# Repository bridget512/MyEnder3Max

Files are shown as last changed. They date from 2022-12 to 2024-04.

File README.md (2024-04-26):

# MyEnder3Max (2020 model)

!! DO NOT JUST COPY CONFIGURATIONS TO YOUR PRINTER AND EXPECT IT TO BE OK !!

Read through the files and make sure they are suitable for YOUR machine. I'm constantly changing and modifying the machine so configurations are specific to MY machine.

Please be careful, and I hope you find something useful :)

### Do your own calibrations for: 
- PID tuning, Z-Offset, Extruder E-steps/rotation, Pressure Advance. (Recommend OrcaSlicer Calibration methods)
- InputShaper, BLTouch XY offset
- Check stepper motor current. Stock: XYZ = 0.580, E = 0.650

## Modifications - Hardware
- BigTreeTech SKR Mini E3 Version 3.0
- Klipper Firmware on a Raspberry Pi 3b running Fluidd UI + rPi camera
- BL Touch v3.1: "Auto Bed Leveling"
- Belted-Z modification using Dual Steppers on a Single Driver. Based on 2 Voron M4 Extruder Kits and adapted for use on the Z-Axis.
- Belted-Z plate accepts a Voron M4 Extruder to be attached using two printable standoffs that also hold the X-Axis umbilical cables.
- Switchwire based Y-Axis modification. Adapted to use a geared 20T GT2 6mm Pulley and M5 bolt.
- Voron M4 Extruder
- Bi-Metal HeatBreak: Generic $20 (Titanium + Copper) w/standard creality heatsink
- HeroMe 7 Hotend Cooler w/Noctua 4020 Fan
- HeroMe 7 5015 Dual Part Cooler
- All printed parts using ASA

## Modifications - Software and Other
- KAMP - Adaptive bed leveling that runs at the begining of every print for perfect bed mesh's where you're printing.
- InputShaper: ADXL345 + Calibration Macros.
- Firmware Retraction [Must also be enabled in slicer. Cura needs a plugin]: Realtime fine tuning of retraction settings.
- Exclude Object [Objects must be labeled in slicer]: Allows individual objects being printed to be excluded from future printing moves. 
- Creality Enclosure - Large (Fabric)
- Raspberry Pi Camera - Auto feed start via script

## Disabled Features:
- Filament Runout (Remove comments to re-enable)

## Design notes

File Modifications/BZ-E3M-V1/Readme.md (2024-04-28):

# M4 Belted Z Modification - V1R1

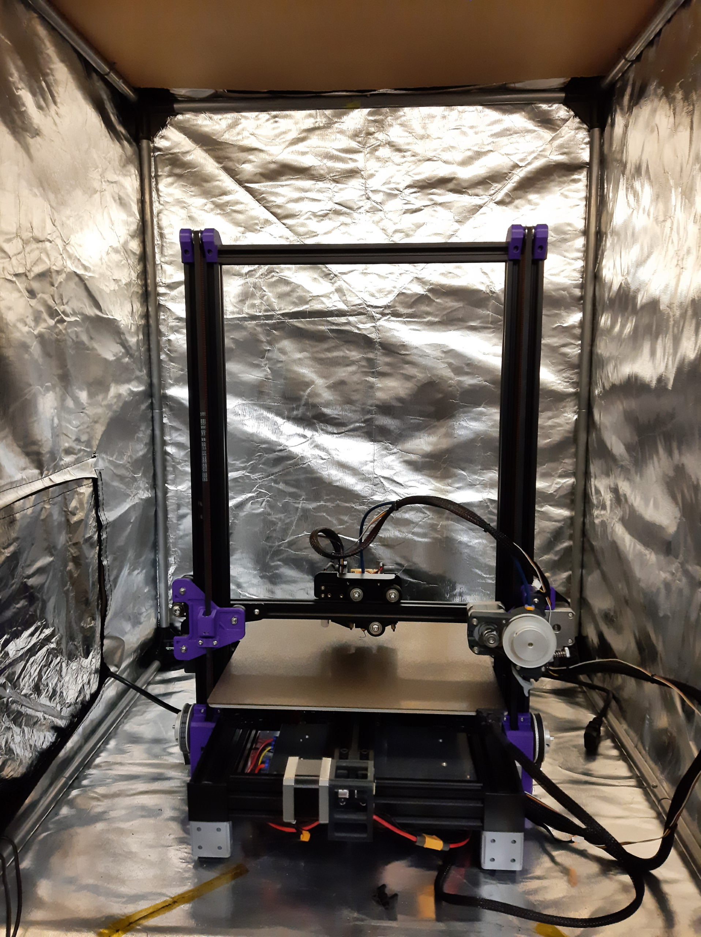
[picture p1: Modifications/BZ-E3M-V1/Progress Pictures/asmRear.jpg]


## Components Used:
- 2x Voron M4 Extruder Kits
    - Uses some of the parts (Bearings, some screws, 80t drive gear pulley and screws).
    - Spare extruder gears are great when printing CF filaments as they get worn down! ;)
    - Future versions will use more of the parts in the kit.
- 2x 60mm x 5mm D-Shafts (Voron 2.4 Z-Drive/D-Axis Kit)
    - Currently using these shafts instead of the extruder kit shafts due to the shaft notches being in awkward spots. 
- 2x 30mm x 5mm dowel pins
    - These are used for the top pulleys.
- 28x 5mmID x 1mm spacers
    - Future versions will use printed spacers.
- Pulleys:
    - 2x Idler Pulley - GT2, 20 Teeth, 5mm Bore, 6mm Width .
    - 2x Timing Pulley Sprocket - GT2, 20 Teeth, 5mm Bore, 6mm Width (+2 if printing 80t reduction gear).
- Screws:
    - 6x M3x6
    - 4x M3x8
    - 4x M3x10
    - 6x M3x12 (2 from M4 Kit)
    - 4x M3x16 (M4 Kit)
    - 4x M3x30 (M4 Kit)
    - 2x M3x35
    - 3x M5x40
- Belt: 2m GT2 Gates 6mm wide

# BZ-V1 Assembly Notes 
Please note that this is not a completed modification and is very much a mixture of parts. 

The following notes were taken when assembling the kit and will be used to make modifications to the parts for future revisions.

## Material and Settings
 - Material: ASA - Purple Siddament. 
 - Temps: H:255c, B: 98.
 - Part: 4 Walls, 5 Tops/Bottoms, 40% infill.
 - Speeds: 60mm/s walls/infill, 40mm/s default.
 - Accelerations: 1500-3000.

## BZ-MP (Motor Plates)
- Access slot for pulley should be relocated to the side (bottom access is difficult)
- Mating Faces to extrusion must be filed flat due to print orientation
- Slight movement from assembly body once mounted. This is fine.
 ### Components (Per Side)
  - 2pc M3x12, 1pc M3x6
  - Spacers 5 + 5 + 4

## BZ-M4 & BZ-R (V-Wheel Plates)
 - V-Roller Holes and Nut too small by ~0.08ish
 - Heat-Set threads not deep enough by 0.8 - 1.0mm.
 - Belt adjuster captive nut hole too small in all directions, including inner hex shape.
 - Fillet on belt adjuster causing overhang issues, make them square.
 ### Components
  - 3pc M5x40
  - 8.4mm worth of spacers (they're usually not accurate, I have 9pcs of 1mm spacers that measure 8.42mm)
  - Belt Adjuster: 1pc M3x16, 2pc M3x10

## BZ-Idlers
 - Extrusion sizing could be slightly bigger for easier fitment.
 ### Components (Per Side)
  - 1pc 30mm x 5mm dowel pin
  - 2pc M3x6, 2pc M3x8
  - 4pc M3 T-Slot Nuts

## BZ-M4-Risers
 - M3 hole too small. 

## BZ-M4-Riser-CableClamps
 - Slight layer drooping on M3 hole from overhang due to print orientation. Hole needs to be filled or enlarged in the model.
 ### Components (Per Riser)
  - 1pc M3x35

## Belt Used
- 198.5mm - 6mm - GT2 Gates

# Images
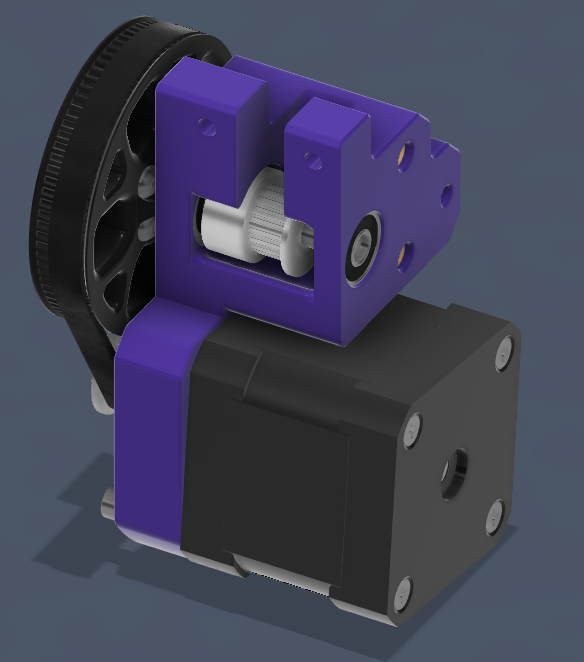
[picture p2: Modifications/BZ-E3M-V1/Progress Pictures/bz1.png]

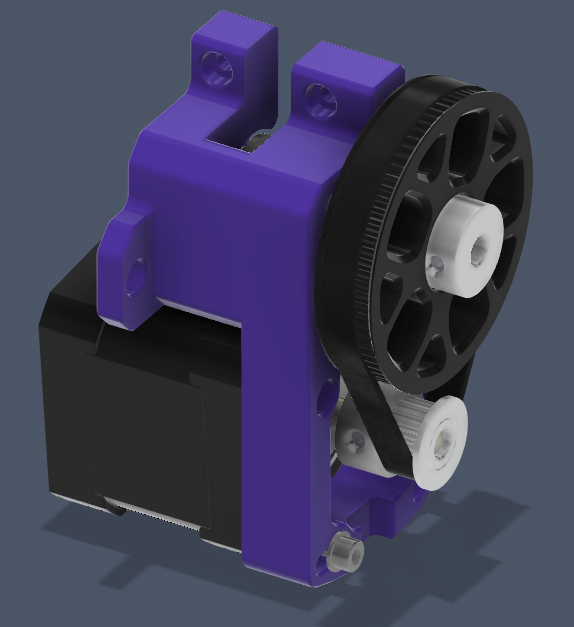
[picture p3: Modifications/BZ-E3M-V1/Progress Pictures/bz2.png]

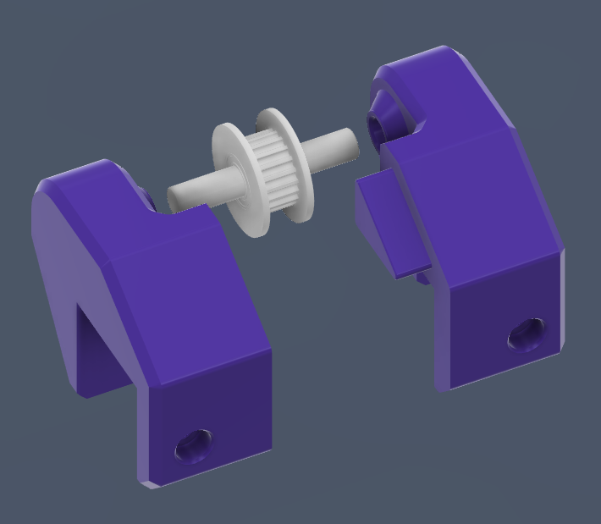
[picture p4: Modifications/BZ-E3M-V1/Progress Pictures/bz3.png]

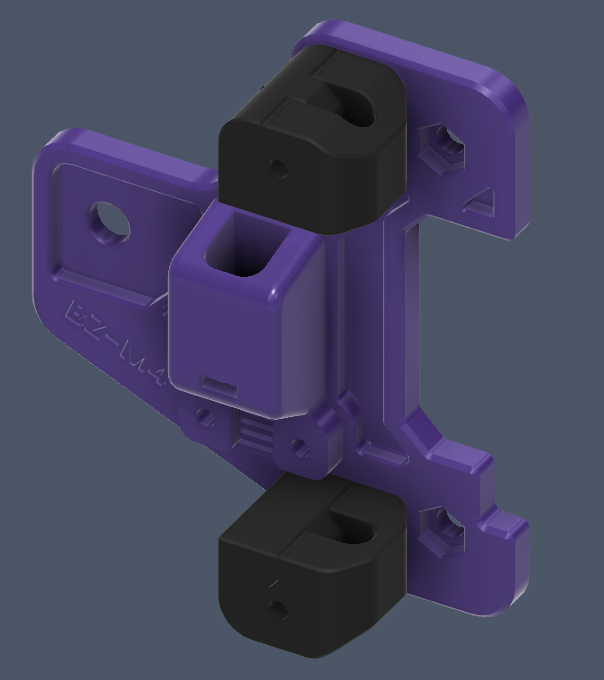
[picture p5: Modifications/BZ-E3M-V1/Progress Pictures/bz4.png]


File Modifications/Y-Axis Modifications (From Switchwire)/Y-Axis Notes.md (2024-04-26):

## Y axis
- less belt length is needed than the standard E3Max. Re-crimping the belt is necessary 

## Y axis rear notes

- The stepper attached pulley must be removed to tighten a mounting bolt placed behind the pulley.

- The motor mount bracket is very close to the build plate. It is possible that the insulation underneath the bed can catch on the bracket and pull it back. I recommend using kapton tape to stick this down to make this less likely. 

- I have concerns of heat related part failure, or parts becoming loose due to printed parts compressing and losing tension over time due to extra heat in the area.

## Y Axis Front

- ender3v2 switchwire conversion issue: Pulley bolt is an M5 bolt, the E3Max uses a M3 bolt. Modifying the adjustable carriage is needed to use this hardware. Alternatively, purchasing an idler pulley with a larger internal diameter would work.

- Slipping the belt into the printer bed plate can be difficult as there is little slack when the Y-Axis is fully assembled. Removing the front assembly, leaving the idler-pulley part attached, and bringing the bed forward makes this much easier to access and gives adequate slack.

- The current offset of the Idler body part is about 4cm shorter than the standard bracket. This reduces the amount of movement the y axis can slide on, resulting in ~4cm of build area being removed on this axis.

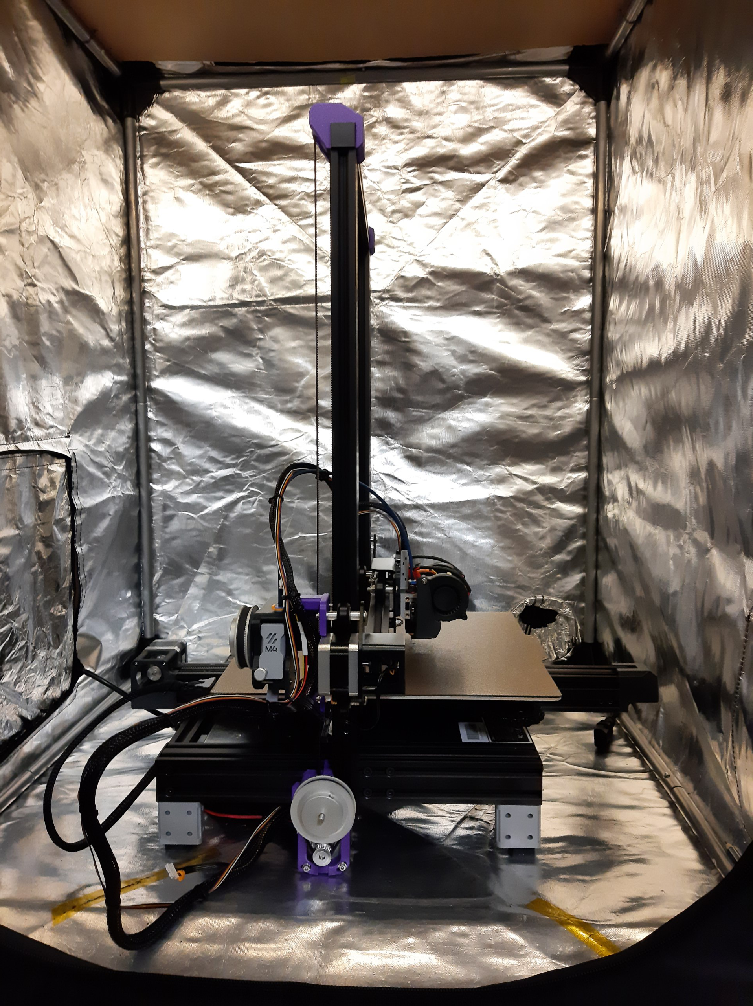
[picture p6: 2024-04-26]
Modifications/BZ-E3M-V1/Progress Pictures/asmLeft.jpg

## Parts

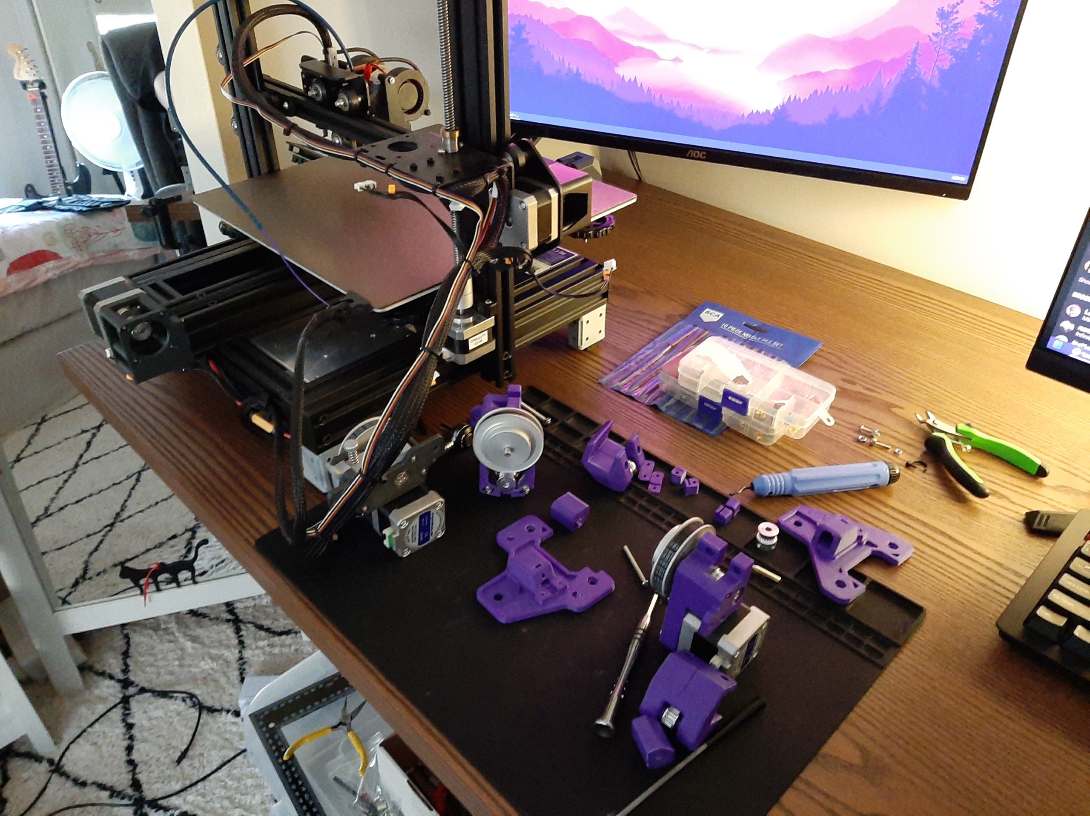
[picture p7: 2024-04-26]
Modifications/BZ-E3M-V1/Progress Pictures/Parts.jpg

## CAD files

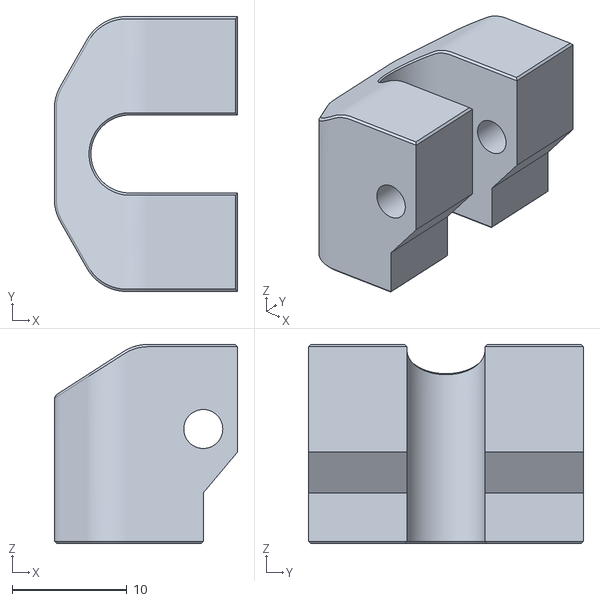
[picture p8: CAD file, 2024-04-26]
Modifications/BZ-E3M-V1/Parts/M4-Riser-CableClamp-Top-Part2.stl
16.0 x 24.0 x 17.4

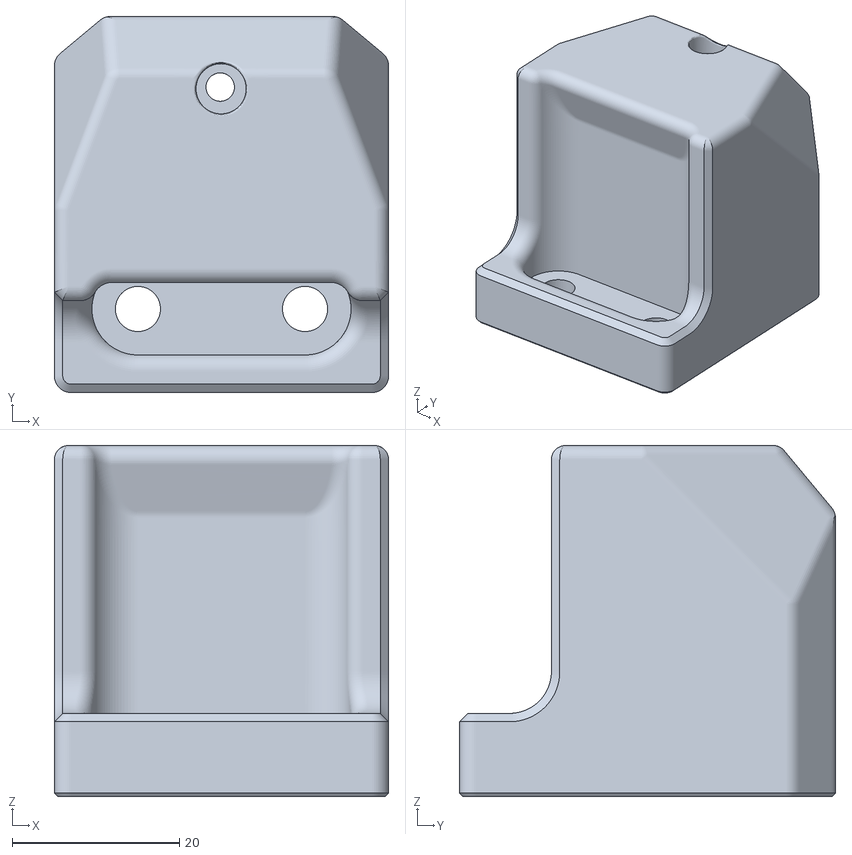
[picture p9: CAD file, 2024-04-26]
Modifications/Y-Axis Modifications (From Switchwire)/STL's/y_idler_a.stl
40.0 x 45.0 x 42.0

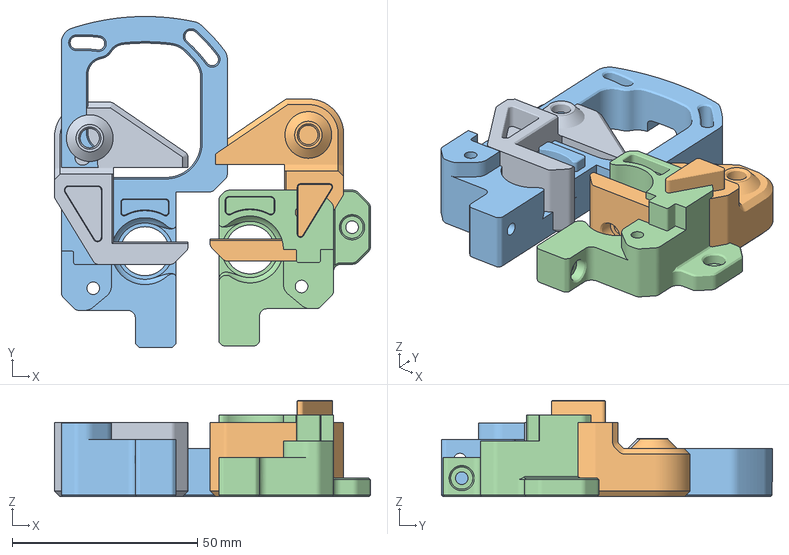
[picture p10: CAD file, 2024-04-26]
Modifications/BZ-E3M-V1/Parts/Z Mod Project.3mf
85.4 x 89.3 x 26.0 mm
TopIdlerBracketA.stl
TopIdlerBracketB.stl
ZMotorPlate_A_BottomLeft.stl
ZMotorPlate_B_BottomLeft.stl

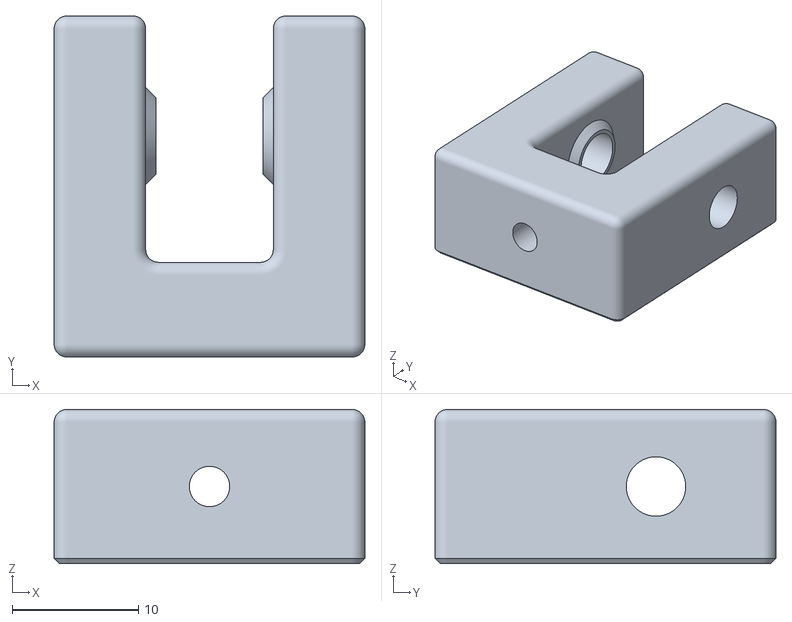
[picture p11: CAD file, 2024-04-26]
Modifications/Y-Axis Modifications (From Switchwire)/STL's/Y-Idler-M5-Geared-0.4WiderForFiling.stl
24.6 x 27.0 x 12.2

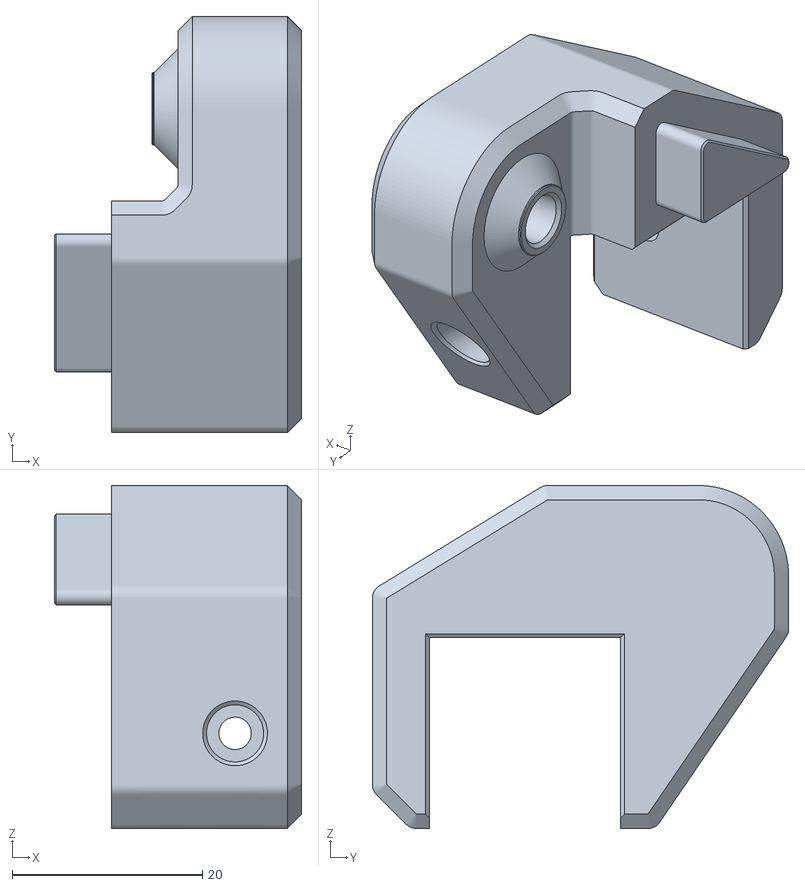
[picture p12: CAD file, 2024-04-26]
Modifications/BZ-E3M-V1/Parts/BZ-Idler-Right.stl
26.0 x 43.8 x 36.0

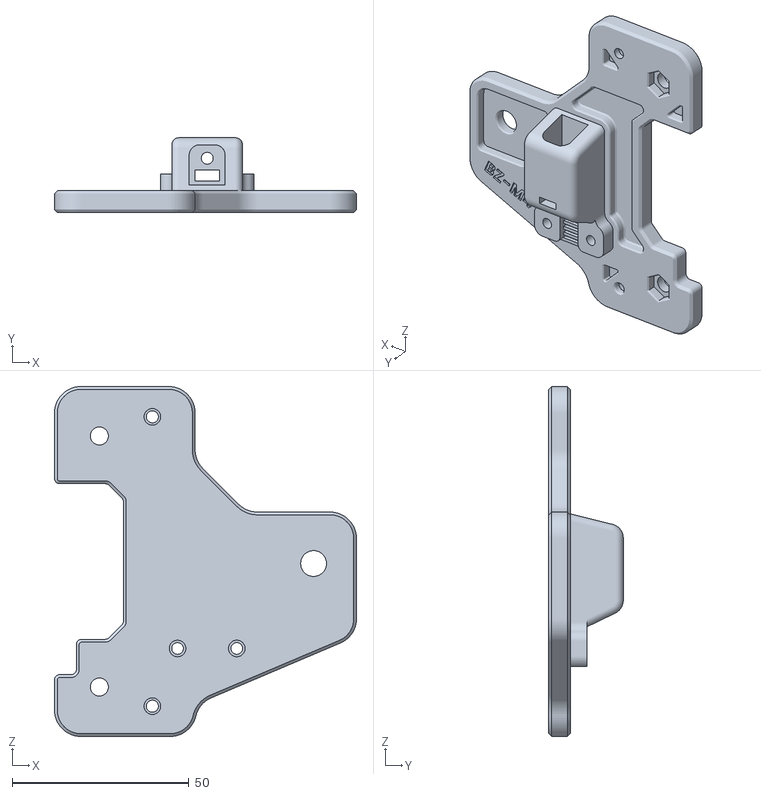
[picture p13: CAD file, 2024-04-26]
Modifications/BZ-E3M-V1/Parts/BZ-M4.stl
85.5 x 21.1 x 99.0

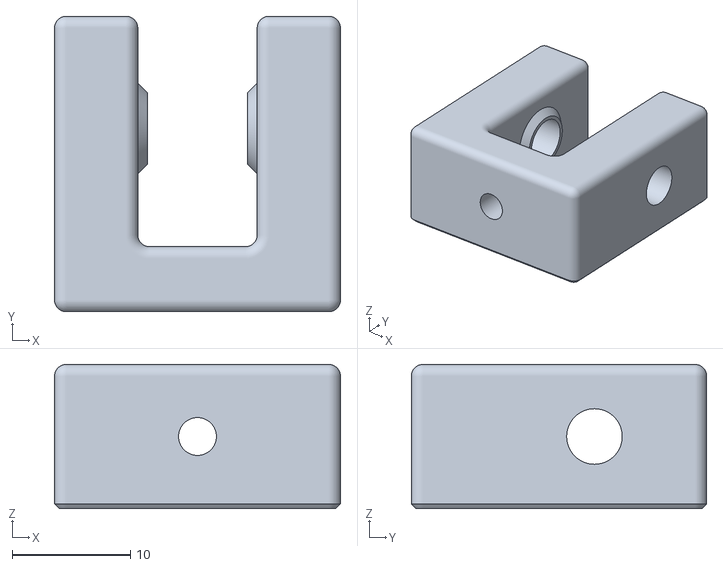
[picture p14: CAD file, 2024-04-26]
Modifications/Y-Axis Modifications (From Switchwire)/STL's/Y-Idler-M5-Geared.stl
24.2 x 25.0 x 12.2

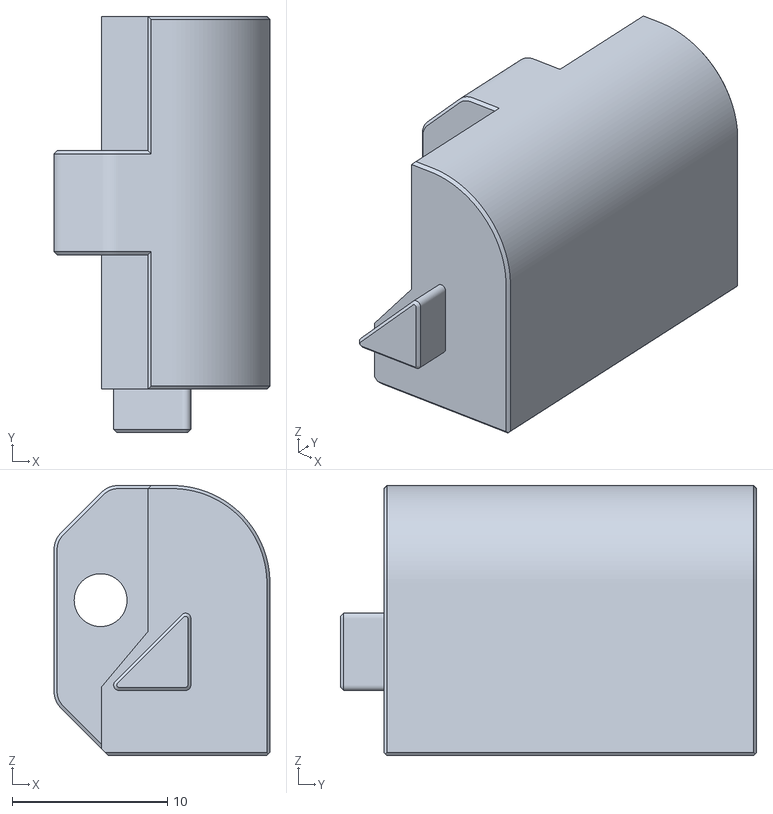
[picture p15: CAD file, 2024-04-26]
Modifications/BZ-E3M-V1/Parts/M4-Riser-CableClamp-Top-Part1.stl
13.9 x 26.8 x 17.4

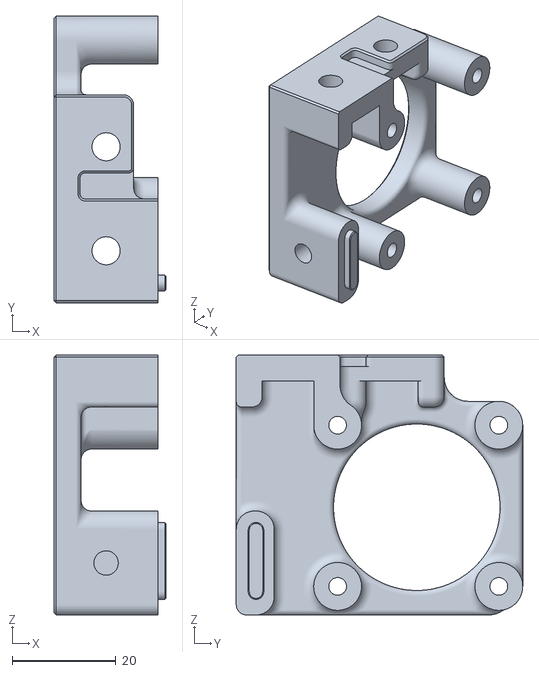
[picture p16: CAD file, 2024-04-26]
Modifications/Y-Axis Modifications (From Switchwire)/STL's/y_motor_mount_a.stl
21.5 x 55.1 x 50.0

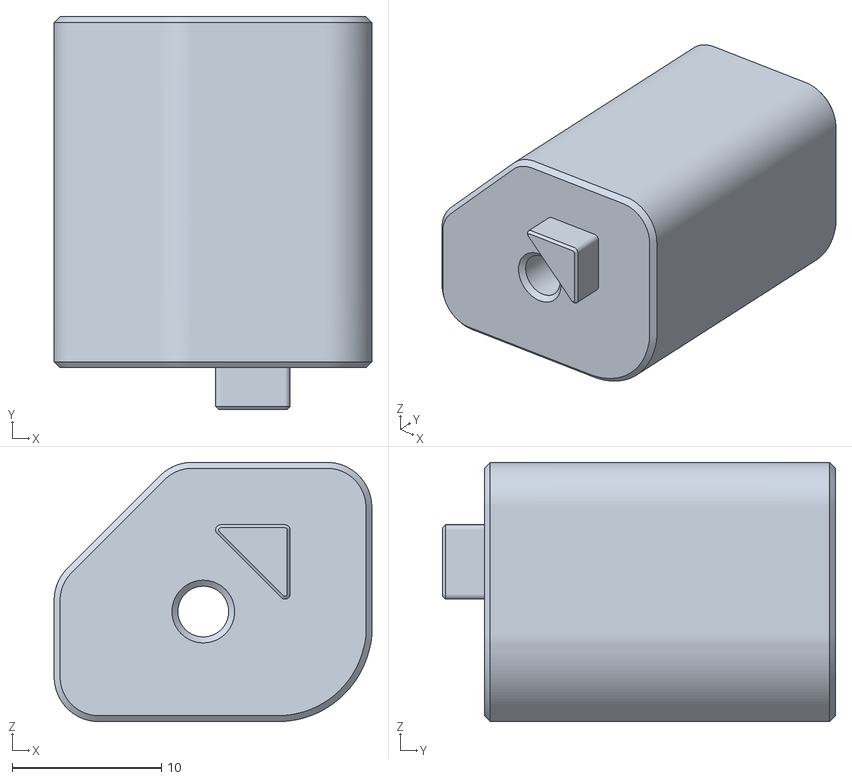
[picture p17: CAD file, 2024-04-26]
Modifications/BZ-E3M-V1/Parts/BZ-M4-RiserBottom.stl
21.3 x 26.3 x 17.4

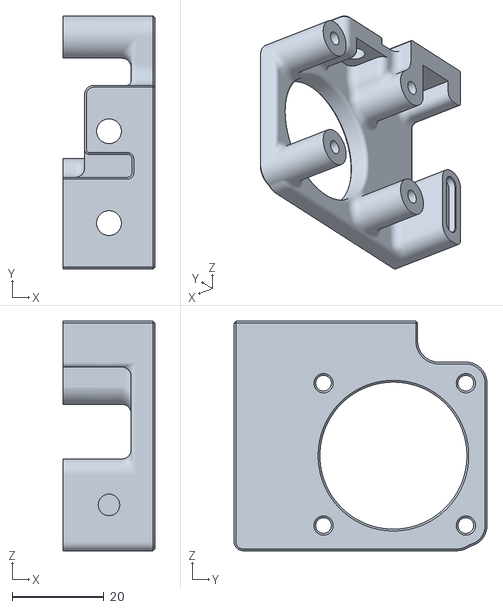
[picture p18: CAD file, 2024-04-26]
Modifications/Y-Axis Modifications (From Switchwire)/STL's/y_motor_mount_b.stl
20.0 x 55.1 x 50.0

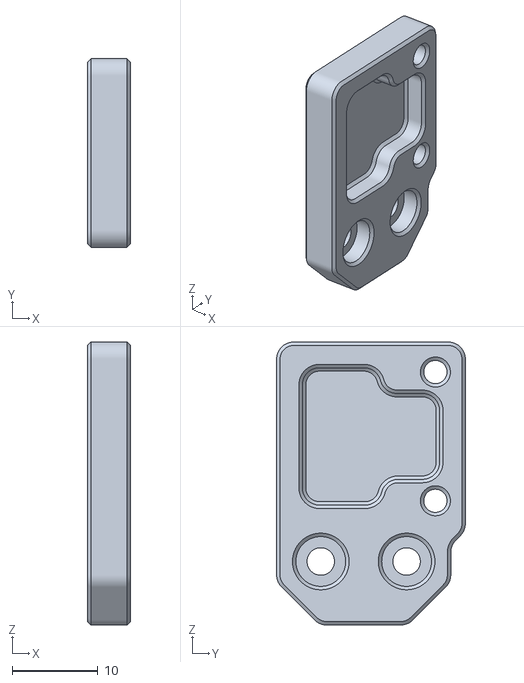
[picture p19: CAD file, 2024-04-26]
Modifications/Y-Axis Modifications (From Switchwire)/STL's/Y-Endstop.stl
5.00 x 22.0 x 33.0

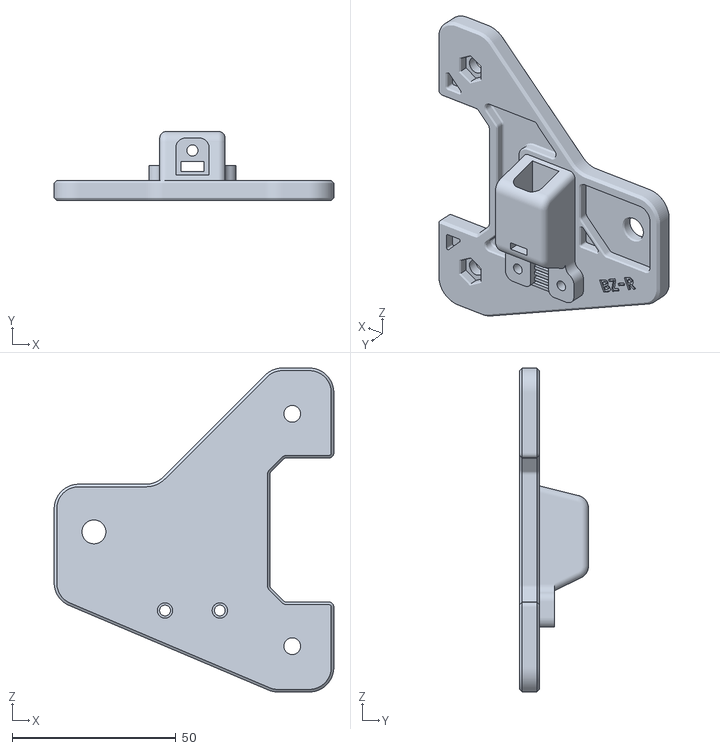
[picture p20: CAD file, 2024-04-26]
Modifications/BZ-E3M-V1/Parts/BZ-R.stl
85.5 x 21.1 x 99.0

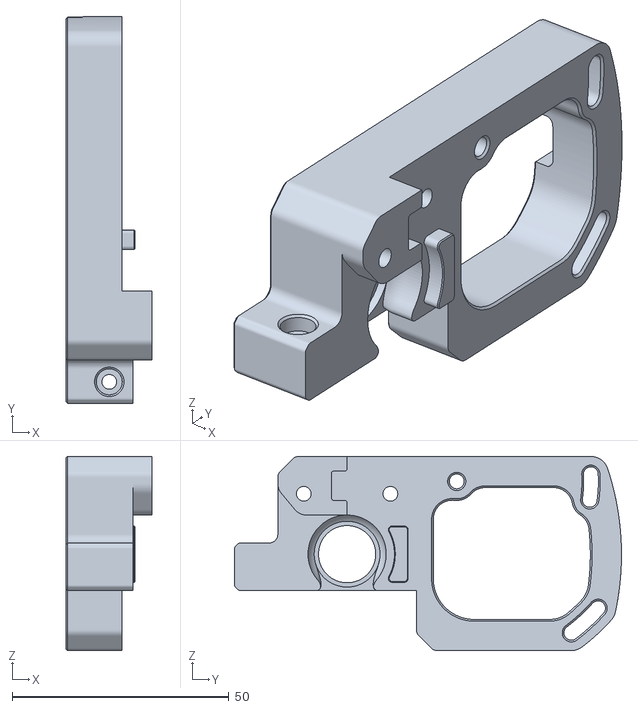
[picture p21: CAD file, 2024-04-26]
Modifications/BZ-E3M-V1/Parts/BZ-MPA.stl
19.9 x 89.3 x 44.8

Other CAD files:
Modifications/BZ-E3M-V1/Parts/M4-Riser-CableClamp-Bottom-Part2.stl
Modifications/BZ-E3M-V1/Parts/M4-Riser-CableClamp-Bottom-Part1.stl
Modifications/BZ-E3M-V1/Parts/ZAdjuster.stl
Modifications/BZ-E3M-V1/Parts/BZ-M4-RiserTop.stl
Modifications/BZ-E3M-V1/Parts/BZ-Idler-Left.stl
Modifications/BZ-E3M-V1/Parts/BZ-MPB.stl
Modifications/BZ-E3M-V1/Parts/BeltClamp.stl
Modifications/Y-Axis Modifications (From Switchwire)/STL's/y_idler_inner_M4 Pulley Bolt Modification PLUS rotated nut.stl

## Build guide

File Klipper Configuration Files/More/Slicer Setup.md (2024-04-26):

# ================================================================
# Slicer Setup
# Author: Bridget512
# ================================================================
- This file contains slicer specific G-Code that is used by the slicer to run macros on the printer.
- Copy and Paste these code snippits to the corrosponding sections in the Custom G-Code sections, usually located in Printer Settings.
- Do not copy any text that starts with ## to the slicer.
- Some G-Code will be the same, usually End G-Code, but some slicers use their own settings to reference and are used in the G-Code for that slicer.
# ================================================================

# ================================================================
# PrusaSlicer (2.4.0 to Newest)
# ================================================================

## Start G-Code Section
SET_PRINT_STATS_INFO TOTAL_LAYER=[total_layer_count]    ; Reports total layers to klipper. Used to display layer information on the printers display.
_PRINT_START EXTRUDER_TEMP=[first_layer_temperature] BED_TEMP=[first_layer_bed_temperature]

## End G-Code Section
_PRINT_END

## After layer change G-Code
SET_PRINT_STATS_INFO CURRENT_LAYER={layer_num + 1}
;M117 Layer {layer_num+1}/[total_layer_count]

# ================================================================
# SuperSlicer
# ================================================================

## Start G-Code
;SET_RETRACTION_BY_MATERIAL_TYPE MATERIAL_TYPE=[filament_type]
SET_PRINT_STATS_INFO TOTAL_LAYER=[total_layer_count]    ; Reports total layers to klipper. Used to display layer information on the printers display.
_PRINT_START EXTRUDER_TEMP={first_layer_temperature+extruder_temperature_offset} BED_TEMP=[first_layer_bed_temperature]

#End G-Code
_PRINT_END

## After layer change G-Code
SET_PRINT_STATS_INFO CURRENT_LAYER={layer_num + 1}
;M117 Layer {layer_num+1}/[total_layer_count]

# ================================================================
# OrcaSlicer
# ================================================================

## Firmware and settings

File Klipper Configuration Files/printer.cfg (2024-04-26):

# ================================================================
# Klipper + Fluidd printer.cfg
# ================================================================
# Author: Bridget512
# Printer: Creality Ender 3 MAX 2020
# Mainboard: BigTreeTech SKR Mini E3 Version 3.0 (STM32G0B1, 8KiB bootloader (stm32duino), 8 MHz crystal, USB (on PA11/PA12))
# Modifications: BL Touch v3.1, Voron M4 Extruder (w/StepperOnline 17HS15-1504S), Bi-Metal HeatBreak, HeroMe7 base with modified part-cooling
# Modifications cont...: Voron Y-Axis (needs cad modification for full bed), Custom Voron M4 extruder gearbox based Z-Axis (w/StepperOnline 17HS15-1504S)
# ================================================================

# ================================================================
# Klipper Setup
# ================================================================
[virtual_sdcard]
path: ~/gcode_files
[display_status]
[pause_resume]
[exclude_object]

# ================================================================
# Includes
# ================================================================
[include macros.cfg]
[include display.cfg]
[include features.cfg]
[include KAMP_Settings.cfg]

# ================================================================
# Microcontrollers
# ================================================================
[idle_timeout]
# Description: Prevents heater from switching off on long bed/chamber pre-heats
timeout: 1200                            # Default: 600 Seconds (10 Minutes)

[mcu]
# Run "ls /dev/serial/by-id/*" for micro-controller name
serial: /dev/serial/by-id/usb-Klipper_stm32g0b1xx_07002A001750425938323120-if00
restart_method: command

[mcu rpi]
serial: /tmp/klipper_host_mcu

[temperature_sensor Mainboard]
sensor_type: temperature_mcu
min_temp: 10
max_temp: 100

[temperature_sensor raspberry_pi]
sensor_type: temperature_host
min_temp: 10
max_temp: 100

# # Allows movement without having to home. Can be dangerous.
# # [force_move]
# # enable_force_move: True

# ================================================================
# Hotend, Extrusion, and Bed
# ================================================================
[extruder]
step_pin: PB3
dir_pin: !PB4
enable_pin: !PD1
heater_pin: PC8
sensor_type: EPCOS 100K B57560G104F
sensor_pin: PA0
filament_diameter: 1.750
nozzle_diameter: 0.4
pressure_advance: 0.40                   # Standard Nozzle: 0.5, Brass CHT 0.4mm: 0.38
microsteps: 16
full_steps_per_rotation: 200
min_temp: 0
max_temp: 265                           # DO NOT EXCEED 260*c for printing on the standard thermistor. +5 to prevent error on heating overshoot.
min_extrude_temp: 10                    # Set low for filament loading. 170*c Recommended
max_extrude_only_distance: 400.0
max_extrude_cross_section: 15           # M4 Extruder accel error fix - Default: 0.8
#gear_ratio: 80:20
rotation_distance: 5.500                # Updated: New M4 build April 2024 | Old 5.585

[tmc2209 extruder]
uart_pin: PC11
tx_pin: PC10
uart_address: 3
run_current: 0.650                      # Default Current for Extruder: 0.650 (Stock and StepperOnline)
# stealthchop_threshold: 999999         # Stealthchop is disabled as it creates a loud grinding noise on fast movements. It's especially bad with pressure advance on.

[heater_bed]
heater_pin: PC9
sensor_type: ATC Semitec 104GT-2
sensor_pin: PC4
min_temp: 0
max_temp: 105                           # DO NOT EXCEED 100*c for printing. +5 to prevent error on heating overshoot.

# ================================================================
# Printer and Steppers 
# ================================================================
[printer]
kinematics: cartesian
max_velocity: 300
max_accel: 2500
minimum_cruise_ratio: 0.5
max_z_velocity: 12
max_z_accel: 100

[stepper_x]
step_pin: PB13
dir_pin: !PB12
enable_pin: !PB14
microsteps: 64                         # StealthChop = 16 | SpreadCycle = 64 or 128 
rotation_distance: 40
endstop_pin: ^PC0
position_min: -2.5
position_endstop: -2.5
position_max: 302.5
homing_speed: 80

[tmc2209 stepper_x]
uart_pin: PC11
tx_pin: PC10
uart_address: 0
run_current: 0.580
interpolate: False                      # Use higher microstepping instead for SpreadCycle
# stealthchop_threshold: 999999         # https://github.com/Klipper3d/klipper/blob/master/docs/TMC_Drivers.md

[stepper_y]
step_pin: PB10
dir_pin: PB2
enable_pin: !PB11
microsteps: 64                          # StealthChop = 16 | SpreadCycle = 64 or 128
rotation_distance: 40
endstop_pin: ^PC1
position_min: -20
position_endstop: -20
position_max: 270                       # Default for Max: 320. Temporary Switchwire Y-Axis fix: 270
homing_speed: 80

[tmc2209 stepper_y]
uart_pin: PC11
tx_pin: PC10
uart_address: 2
run_current: 0.600                      # Default Current for Stock Creality Y Stepper: 0.580
interpolate: False                      # Use higher microstepping instead for SpreadCycle
# stealthchop_threshold: 999999         # Y axis max accel with stealthchop = 3000mm/2 before skipping | https://github.com/Klipper3d/klipper/blob/master/docs/TMC_Drivers.md

[stepper_z]
step_pin: PB0
dir_pin: PC5
enable_pin: !PB1
microsteps: 64                          # Default of 16 worked fine in SpreadCycle
rotation_distance: 40                   # Belted Z 80T and 20T pulleys | Standard Leadscrew: 8
gear_ratio: 80:20                       # Belted Z 80T and 20T pulleys
endstop_pin: probe:z_virtual_endstop
position_min: -4                        # You want this to be lower than your first layer offset, but high enough that if a crash happens the machine will stop (Only works after initial home)
position_max: 300

[tmc2209 stepper_z]
uart_pin: PC11
tx_pin: PC10
uart_address: 1
run_current: 0.580
interpolate: False
# stealthchop_threshold: 999999

[safe_z_home]
home_xy_position: 150, 150
speed: 60
z_hop: 10
z_hop_speed: 40

# ================================================================
# Fans
# ================================================================
# Mainboard:        Wired to Powersupply (24v) > Adjustable buck converter (@12v) > Fan
# Hotend:           Wired to mainboard (24v) > Adjustable buck converter (@12v) > Fan
# PartCooling:      Each connected to their own pins on the mainboard.
# ================================================================

# Hotend Fan - NF-A4x20
[heater_fan heatbreak_cooling_fan]
pin: PB15                               # Fan2 Header
heater: extruder
heater_temp: 50.0

# Part Cooling - ARX Ceradyna 5115 blower fan (Ceramic Sleeve)
# Creates a fan array
[multi_pin part_cooler_pins]
pins: PC6, PC7                          # Fan0, Fan1 Header

[fan]
pin: multi_pin:part_cooler_pins
max_power: 1.0
cycle_time: 0.080 						# 0.080 Time in seconds for each PWM power cycle. Default: 0.010 ## Octoprint Setting: 0.100 ## Fluidd Setting: 0.080 
kick_start_time: 0.150 				    # 0.150 Seconds. Default: 0.100
off_below: 0.15 						# 0.15 Fans turn off at 15% (These ARX fans stop spinning below this anyway)


# ================================================================
# My unused MCU code
# ================================================================
# [mcu pico]
# serial: /dev/serial/by-id/usb-Klipper_rp2040_E66008830742712A-if00
# restart_method: rpi_usb

# [gcode_button pico_EmergencyStop]
# pin: ^!pico:gpio16
# press_gcode: {action_emergency_stop()}
# release_gcode:

# [gcode_button pico_Home]
# pin: ^!pico:gpio15
# press_gcode: G28
# release_gcode:

# [gcode_button pico_move_Z_Up]
# pin: ^!pico:gpio14
# press_gcode: 
#     G91
#     # SET_KINEMATIC_POSITION Z=0
#     G1 z10 F1200
#     G90
#     # M84
# release_gcode:

#*# <---------------------- SAVE_CONFIG ---------------------->
#*# DO NOT EDIT THIS BLOCK OR BELOW. The contents are auto-generated.
#*#
#*# [bed_mesh default]
#*# version = 1
#*# points =
#*# 	0.000000, -0.021875, -0.028125, 0.009375, 0.090625
#*# 	0.025000, -0.018750, -0.025000, 0.000000, 0.034375
#*# 	0.000000, 0.009375, -0.037500, 0.003125, 0.012500
#*# 	0.003125, -0.037500, -0.031250, -0.043750, 0.012500
#*# 	0.003125, -0.009375, -0.078125, -0.043750, -0.056250
#*# tension = 0.2
#*# min_x = 124.31
#*# algo = lagrange
#*# y_count = 5
#*# mesh_y_pps = 2
#*# min_y = 102.83
#*# x_count = 5
#*# max_y = 207.79
#*# mesh_x_pps = 2
#*# max_x = 211.11
#*#
#*# [bltouch]
#*# z_offset = 3.087
#*#
#*# [extruder]
#*# control = pid
#*# pid_kp = 27.152
#*# pid_ki = 1.602
#*# pid_kd = 115.056
#*#
#*# [heater_bed]
#*# control = pid
#*# pid_kp = 75.410
#*# pid_ki = 1.341
#*# pid_kd = 1060.459
#*#
#*# [input_shaper]
#*# shaper_type_x = mzv
#*# shaper_freq_x = 68.6
#*# shaper_type_y = mzv
#*# shaper_freq_y = 33.0

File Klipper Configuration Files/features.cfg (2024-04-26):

# ================================================================
# Features
# - BLTouch + bed mesh
# - Bed Tramming Assistant
# - Firmware Retraction
# - Input Shaper and Accelerometer
# - Filament Runout Sensor
# ================================================================

# ================================================================
# BLTouch and Bed Mesh
# ================================================================
[bltouch]
sensor_pin: PC14
control_pin: PA1
pin_up_touch_mode_reports_triggered: True
stow_on_each_sample: False
probe_with_touch_mode: True
x_offset: 49.7                          # X axis offset from the nozzle. Left[-] and Right[+]
y_offset: -1.8                        	# Y axis offset from the nozzle. Backwards[-] and Forwards[+]
samples: 1
sample_retract_dist: 10.0      
samples_tolerance_retries: 0        	# Can be set lower, example 2.5 depending on height of bltouch from bed
lift_speed: 60
speed: 60

[bed_mesh]
speed: 150                            	# Default: 50
mesh_min: 55, 55                      	# Default: 50, 0
mesh_max: 250, 250                    	# Default: 290, 290
algorithm: bicubic
probe_count: 8, 8                   	# Default: 7,7
horizontal_move_z: 10
fade_start: 1
fade_end: 10
fade_target: 0

# ================================================================
# Bed Tramming Assistant
# ================================================================
[screws_tilt_adjust]
# Screws_Tilt_Adjust can be started by using the button located in the Tools drop down located in the Tool section of the homepage.
# The probe is not able to reach the screw locations on the left of the bed on the Ender3Max.
# These positions will not probe the screw locations making the screw correction values slightly incorrect. Use them as a reference.
screw1: 0, 30
screw1_name: Front Left
screw2: 200, 30
screw2_name: Front Right
screw3: 200, 250
screw3_name: Rear Right
screw4: 0, 250
screw4_name: Rear Left
horizontal_move_z: 10
speed:120
screw_thread: CW-M4

# ================================================================
# Firmware Retraction
# <Nozzle> + <Filament> = <rLength>, <rSpeed>, <unrSpeed>, <unrxLength>
# 0.40 + PLA Polymaker PolyLite = 2.0, 40, 40, 0
# 0.40 + ASA/ABS = 1.95, 35, 35, 0
# 0.25 + eSun ePLA ST = 1.9, 40, 40, 0
# ================================================================
[firmware_retraction]
retract_length: 1.7                    # Retraction Distance (mm) | TriangleLabs Standard Nozzle: 1.95 | CHT Nozzle: 1.7
retract_speed: 40                       # Retraction Speed (mm/s)
unretract_speed: 40                     # Prime Speed (mm/s)
unretract_extra_length: 0               # Additional Prime Amount (+/- to retract_length)(mm)

# ================================================================
# Input Shaper and Accelerometer
# ================================================================
[adxl345]
cs_pin: rpi:None                        # When attached main RPi
## spi_bus: spi0a                        # When attached to additional MCU (Pico)
## cs_pin: pico:gpio1                    # When attached to additional MCU (Pico)

[resonance_tester]
accel_chip: adxl345
probe_points:
    150, 150, 20                        # X, Y, Z - Position of printhead during resonance testing

# ================================================================
# Filament Runout Sensor
# ================================================================
# [filament_switch_sensor e0_sensor]  
# switch_pin: PC15

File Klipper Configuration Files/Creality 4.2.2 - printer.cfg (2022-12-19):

# ================================================================
# Klipper + Fluidd printer.cfg
# Last Update: 1 December 2022
# ================================================================
# Author: Bridget512
# Printer: Creality Ender 3 MAX
# Modifications: BL Touch v3.1, Voron M4 Extruder, Bi-Metal HeatBreak
# Mainboard: Stock Ender 3 Max (2019) v4.2.2, STM32F103, 28KiB Bootloader, Serial (on USART1 PA10/PA9)
# See docs/Config_Reference.md for a description of parameters.
# 
# ================================================================
# Config Features:
# ================================================================
#   Enabled Features:
#   - BlTouch v3.1: Modified mounting location
#   - InputShaper: ADXL345 + Calibration Macros
#   - Firmware Retraction [Must also be enabled in slicer. Cura needs a plugin]: Realtime fine tuning of retraction settings.
#   - Exclude Object [Objects must be labeled in slicer]: Allows individual objects being printed to be excluded from future printing moves. 
#   
#   Disabled Features:
#   - Filament Runout Sensor
#   
#   Optimised bed leveling:
#   - 4x4 bed mesh. Single sample probe. Faster feedrate for x & y. Faster z height movement feedrate.
#        
#   Custom cancel script:
#   - Home's x axis. Move's y axis forward. Raise's Z. Turns off heaters. Turns off part cooling. Disable's all steppers.
#     
# ================================================================
# Klipper Setup
# ================================================================
[virtual_sdcard]
path: ~/gcode_files

[display_status]

[pause_resume]

[exclude_object]

# ================================================================
# Includes
# ================================================================
[include macros.cfg]

# ================================================================
# Microcontrollers
# ================================================================
[mcu]
# Run "ls /dev/serial/by-id/*" for micro-controller name
serial: /dev/serial/by-id/usb-1a86_USB_Serial-if00-port0
restart_method: command

[mcu rpi]
serial: /tmp/klipper_host_mcu

[temperature_sensor Mainboard]
sensor_type: temperature_mcu
min_temp: 10
max_temp: 100

[temperature_sensor raspberry_pi]
sensor_type: temperature_host
min_temp: 10
max_temp: 100

# ================================================================
# Input Shaper and Accelerometer
# ================================================================
[adxl345]
cs_pin: rpi:None

[resonance_tester]
accel_chip: adxl345
probe_points:
    150, 150, 20                        # X, Y, Z - Position of printhead during resonance testing

# ================================================================

[printer]
kinematics: cartesian
max_velocity: 300
max_accel: 2500
max_accel_to_decel: 2500
max_z_velocity: 5
max_z_accel: 100

[stepper_x]
step_pin: PC2
dir_pin: PB9
enable_pin: !PC3
microsteps: 16
rotation_distance: 40
endstop_pin: ^PA5
position_endstop: 0
position_max: 300
homing_speed: 60

[stepper_y]
step_pin: PB8
dir_pin: PB7
enable_pin: !PC3
microsteps: 16
rotation_distance: 40
endstop_pin: ^PA6
position_endstop: 0
position_max: 300
homing_speed: 60

[stepper_z]
step_pin: PB6
dir_pin: !PB5
enable_pin: !PC3
microsteps: 16
rotation_distance: 8
endstop_pin: probe:z_virtual_endstop
position_min: -2.4                      # You want this to be lower than your first layer offset, but high enough that if a crash happens the machine will stop (Only works after initial home)
position_max: 300                       # Make sure to account for new toolhead setups!

[safe_z_home]
home_xy_position: 150, 150
speed: 50
z_hop: 10
z_hop_speed: 50

# ================================================================
# BLTouch and Bed Mesh
# ================================================================
[bltouch]
sensor_pin: ^PB1
control_pin: PB0
pin_up_touch_mode_reports_triggered: True
stow_on_each_sample: False
probe_with_touch_mode: True
x_offset: 50                          	# X axis offset from the nozzle. Left[-] and Right[+]
y_offset: -6.9                        	# Y axis offset from the nozzle. Backwards[] and Forwards[]
samples: 1
sample_retract_dist: 5.0      
samples_tolerance_retries: 0        	# Can be set lower, example 2.5 depending on height of bltouch from bed
lift_speed: 35
speed: 35

[bed_mesh]
speed: 50                            	# Default: 300
mesh_min: 55, 55                      	# Default: 50, 0
mesh_max: 250, 250                    	# Default: 290, 290
algorithm: bicubic
probe_count: 4, 4                      	# Default: 7,7
horizontal_move_z: 5
fade_start: 1
fade_end: 10
fade_target: 0

# ================================================================
# Firmware Retraction
# ================================================================
[firmware_retraction]
retract_length: 2.0                     # Retraction Distance (mm)
retract_speed: 35                       # Retraction Speed (mm/s)
unretract_speed: 35                     # Prime Speed (mm/s)
#unretract_extra_length: 0              # Additional Prime Amount (+/- to retract_length)(mm)

# ================================================================
# Hotend, Extrusion, and Bed
# ================================================================
[extruder]
max_extrude_only_distance: 400.0
step_pin: PB4
dir_pin: PB3
enable_pin: !PC3
microsteps: 16
# Rotation_Distance Calibration - see https://www.klipper3d.org/Rotation_Distance.html
# PLA : 19.574  +/-0.3                  # 0.4mm nozzle           1:1 ratio extruder gear
# PLA : 5.498                           # 0.6mm nozzle           4:1 M4 Extruder
rotation_distance: 5.580               # 0.4mm nozzle           4:1 M4 Extruder          <<<<<<<<<<<<<<<<<<<<<<<<<<<<<<<<<<<<<<<<<<<< ROTATION DISTANCE
nozzle_diameter: 0.400
filament_diameter: 1.750
heater_pin: PA1
sensor_type: EPCOS 100K B57560G104F
sensor_pin: PC5
min_temp: 0
max_temp: 260                           # 260*c maximum on standard thermistor
pressure_advance: 0.0  
max_extrude_cross_section: 15           # M4 Extruder accel error fix - Default: 0.8

[heater_bed]
heater_pin: PA2
sensor_type: EPCOS 100K B57560G104F
sensor_pin: PC4
min_temp: 0
max_temp: 100

# ================================================================
# Part Cooling - ARX Ceradyna 5115 blower fan
# ================================================================
[fan]
pin: PA0
max_power: 1.0
cycle_time: 0.080 						# Time in seconds for each PWM power cycle. Default: 0.010 ## Octoprint Setting: 0.100 ## Fluidd Setting: 0.080 
kick_start_time: 0.150 				    # Seconds. Default: 0.100
off_below: 0.15 						# Fans turn off at 15% (These stop spinning below this anyway)

[display]
lcd_type: st7920
cs_pin: PB12
sclk_pin: PB13
sid_pin: PB15
encoder_pins: ^PB14, ^PB10
click_pin: ^!PB2

# Filament Runout Sensor - Uncomment if you use this sensor
# [filament_switch_sensor e0_sensor]  
# switch_pin: PA4

#*# <---------------------- SAVE_CONFIG ---------------------->
#*# DO NOT EDIT THIS BLOCK OR BELOW. The contents are auto-generated.
#*#
#*# [bed_mesh default]
#*# version = 1
#*# points =
#*# 	-0.147500, -0.197500, -0.202500, -0.157500
#*# 	-0.145000, -0.187500, -0.165000, -0.105000
#*# 	-0.175000, -0.210000, -0.202500, -0.135000
#*# 	-0.122500, -0.190000, -0.210000, -0.180000
#*# tension = 0.2
#*# min_x = 55.0
#*# algo = bicubic
#*# y_count = 4
#*# mesh_y_pps = 2
#*# min_y = 55.0
#*# x_count = 4
#*# max_y = 250.0
#*# mesh_x_pps = 2
#*# max_x = 250.0
#*#
#*# [bltouch]
#*# z_offset = 1.970
#*#
#*# [extruder]
#*# control = pid
#*# pid_kp = 27.902
#*# pid_ki = 1.604
#*# pid_kd = 121.375
#*#
#*# [heater_bed]
#*# control = pid
#*# pid_kp = 74.357
#*# pid_ki = 1.127
#*# pid_kd = 1226.886
#*#
#*# [input_shaper]
#*# shaper_type_x = mzv
#*# shaper_freq_x = 73.8
#*# shaper_type_y = 2hump_ei
#*# shaper_freq_y = 43.4

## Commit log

2022-12-19 Current custom machine gcode
2022-12-19 Current Klipper Configuration Files
    [Creality 4.2.2 - printer.cfg, display.cfg, features.cfg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]
2022-12-27 endstop update, stepper current lowered
    - Printer endstop positions and origin updated: Now homes closer to the centre of the build plate.
    - Extruder stepper current lowered from 0.650 to 0.625: Attempting to lower stepper heat.
    [printer.cfg]
2022-12-27 Excel document for calculating Extruder eSteps/Rotation
    [eSteps & Rotation Calculator.xlsx]
2023-01-04 Material type retraction settings auto-gcode
    Added a gcode_macro that gets the material type from the slicer gcode and applies the retraction settings for that material type.
    Requires custom start g-code (see macros.cfg for information)
    [macros.cfg]
2023-03-23 Full File update: Minor Changes
    Post SDcard recovery (had corrupt boot partition)
    Changed current for Extruder. Old: 0.650, New: 0.625.
    Lower accelerations (while X gantry is having issues): Old: 2000, New: 1500.
    Adds some rPi Pico test code (disabled)
    PID Tuned for new PEI Build Sheet
    [features.cfg, macros.cfg, printer.cfg]
2023-03-24 SuperSlicer (2.5.59.0) settings update
    Full settings update.
    Conservative speed settings (50mm/s +/- 20%, 1500accel on printer)
    Reliably prints mechanically strong parts while also looking really nice.
2024-04-26 Current Modifications and Setup Update
    Custom M4 Extruder kit Belted Z - Compatible with KevinAkaSam Belted Z Mod.
    Includes M4 Extruder mount and cable retention standoffs.
    Includes modified Switchwire Y Axis files. Modification for M5 bolt and 12mm 20t GT2 Pulley.
    Calibration for re-printed M4 Extruder, CHT Nozzle calibrated pressure advance.
    Now using screw_tilt_calibrate for bed leveling.
    Added excel doc for easy calculation of belt tension frequency.
    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
    [Adaptive_Meshing.cfg, BZ-Idler-Left.stl, BZ-Idler-Right.stl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]
2024-04-27 Updated Extrusion and FlowRate Calculators
    Updates
    - Now includes a section for calculating Flow Ratio of printed flow rate passes from OrcaSlicer.
    - Updated calculator for eSteps used in Marlin firmware, and Rotation_Distance used in Klipper firmware.
    [Extrusion and Flow Ratio Calculators.xlsx, eSteps & Rotation Calculator.xlsx]
2024-04-28 Updated Belted Z Documentation
    [Belted Z Bill Of Materials.xlsx]
2024-04-28 Updated Belted Z Documentation.. again
